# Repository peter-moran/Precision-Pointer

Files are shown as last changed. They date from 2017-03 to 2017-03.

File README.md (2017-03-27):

# Precision Pointer
This repository holds all of the code and hardware files for building a Precision Pointer unit (PPU). This repository is not fully ready to be public, so you may encounter errors or gaps in documentation -- however all the code needed to run the system (other than dependencies) can be found here.

## Building a PPU
Here's the general steps to replicating the system.
1. Buy the materials in `/Hardware Documentation/Bill of materials.csv`
2. Wire and assemble PPU. You will need to create additional mounts for the linear actuator. Again, see the files in the Hardware Documentation folder. See `pointer_driver/pointer_driver.ino` for pin definitions.
3. Connect to ArbotiX in Arduino IDE and upload `pointer_driver.ino`
4. Use `pointer.py` as an API interface to the PPU. `pointer_client.py` is also provided to provide remote control of a PPU connected to a remote machine.

---

# TODO
1. Remove Klampt dependency -- specifically replace `vectorops` operations.
2. Replace servo linear actuator with a digital servo motor. Specifically, use another dynamixel motor and translate the rotational motion to linear motion. This will provide far better consistency and accuracy for linear motion.

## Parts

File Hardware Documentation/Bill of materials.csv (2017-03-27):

Pointer Bill of Materials
Item | Brand | Manufacturer Part # | Source | Link | Count | Unit Price
ScorpionX MX-64 Robot Turret | Trossen Robotics | KIT-SXT-MX64 | Trossen | http://www.trossenrobotics.com/p/ScorpionX-RX-64-robot-turret.aspx | 1 | $749.95
L12 100mm 210:1 Linear Actuator | Firgelli |  | Trossen | http://www.trossenrobotics.com/p/figelli-L12-100mm-210-1-Linear-Actuator.aspx | 1 | $90.00

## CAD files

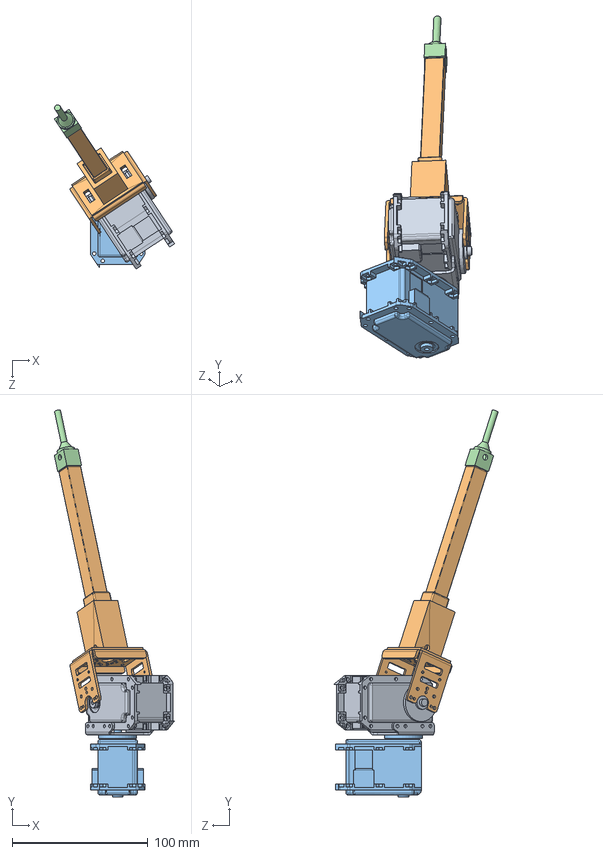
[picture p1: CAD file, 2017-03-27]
Hardware Documentation/Part geometries/Assemblies/Link Assembly.SLDASM
88.6 x 284.9 x 120.9 mm
ppu-link-2
ppu-link-3
MX-64R
IML-PPU-Tip

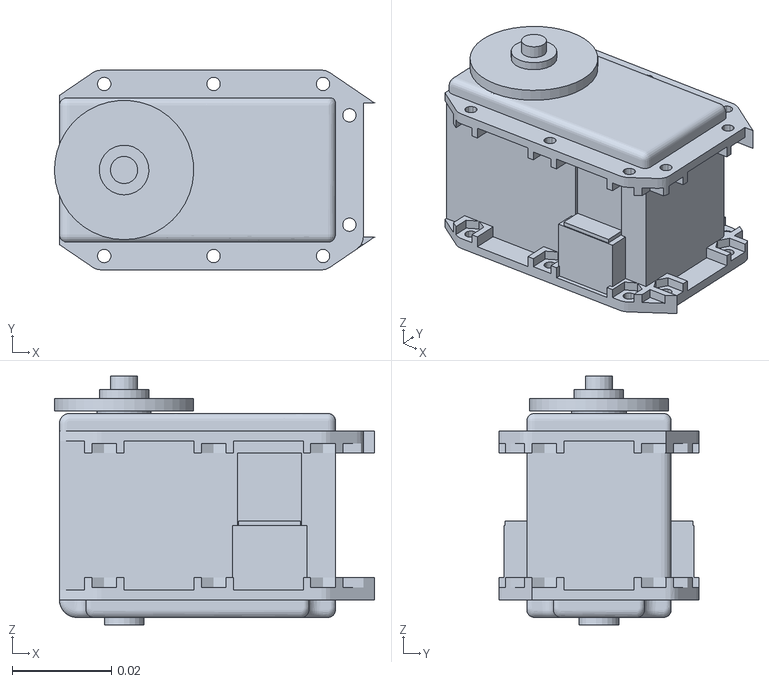
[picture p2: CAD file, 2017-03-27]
Hardware Documentation/Part geometries/Assemblies/Link geometry/ppu-link-1.STL
0.0643 x 0.0402 x 0.05

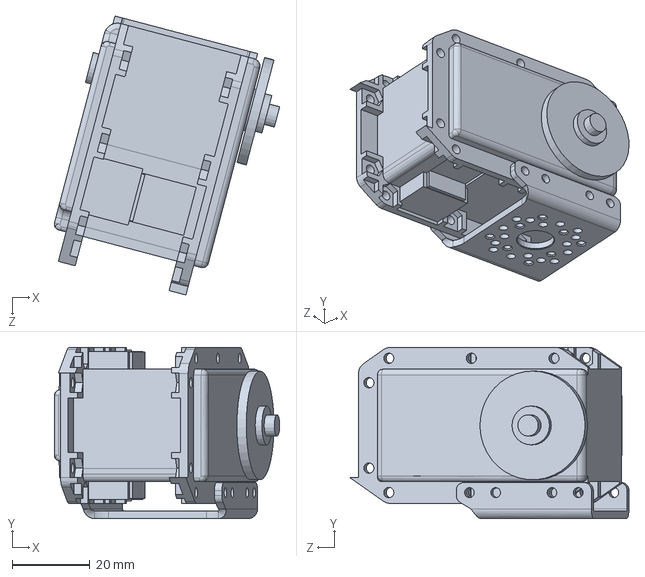
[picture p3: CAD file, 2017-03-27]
Hardware Documentation/Part geometries/Assemblies/Sub-assemblies/ppu-link-2.SLDPRT
58.1 x 44.1 x 71.9 mm

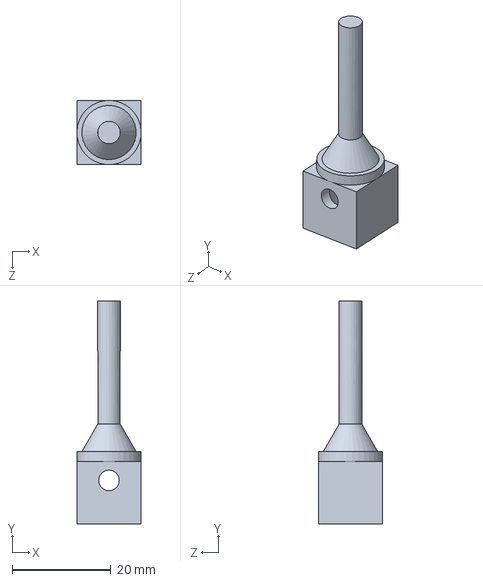
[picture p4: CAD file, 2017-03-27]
Hardware Documentation/Part geometries/Custom Parts/IML-PPU-Tip.SLDPRT
13.0 x 45.2 x 13.0 mm

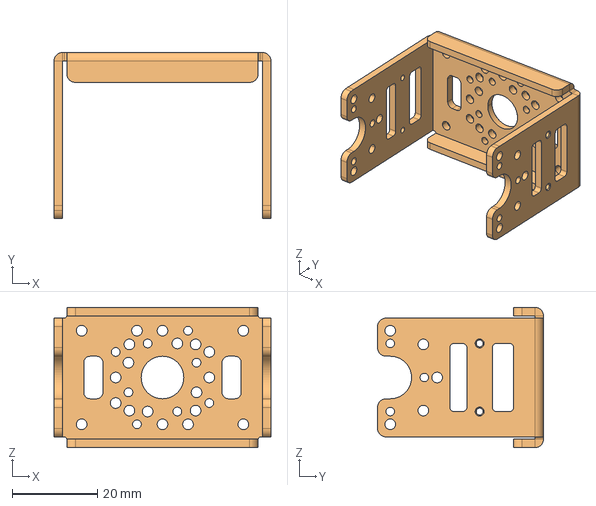
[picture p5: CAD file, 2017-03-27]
Hardware Documentation/Part geometries/Hinge Frame/FR05-H101.stp
51.0 x 39.0 x 33.0 mm

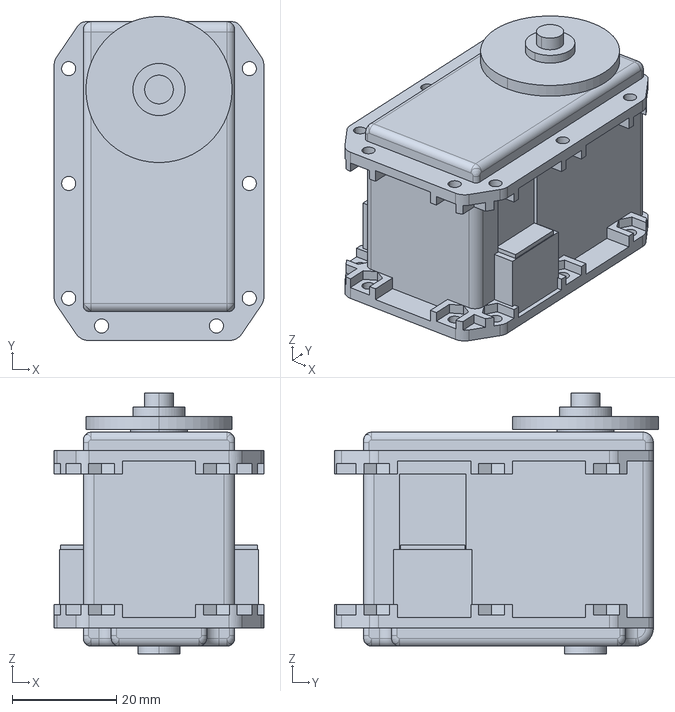
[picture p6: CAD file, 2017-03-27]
Hardware Documentation/Part geometries/MX-64 Servo Motor/MX-64R.stp
40.2 x 62.1 x 50.0 mm

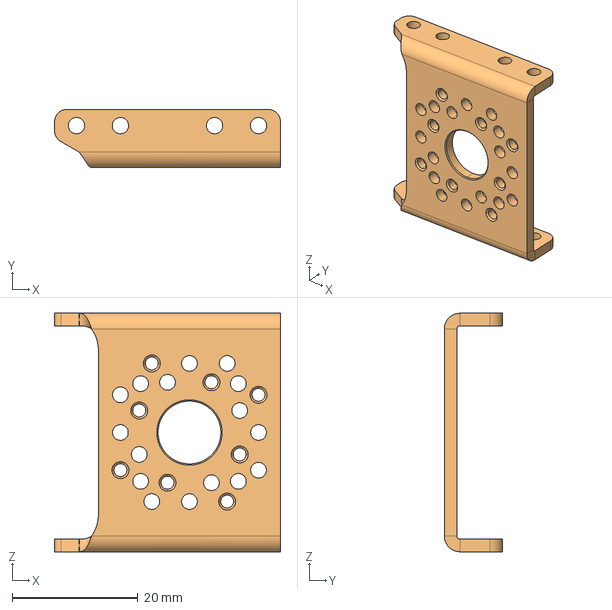
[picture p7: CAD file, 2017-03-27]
Hardware Documentation/Part geometries/Side Frame/FR05-S101.stp
36.0 x 9.30 x 38.0 mm

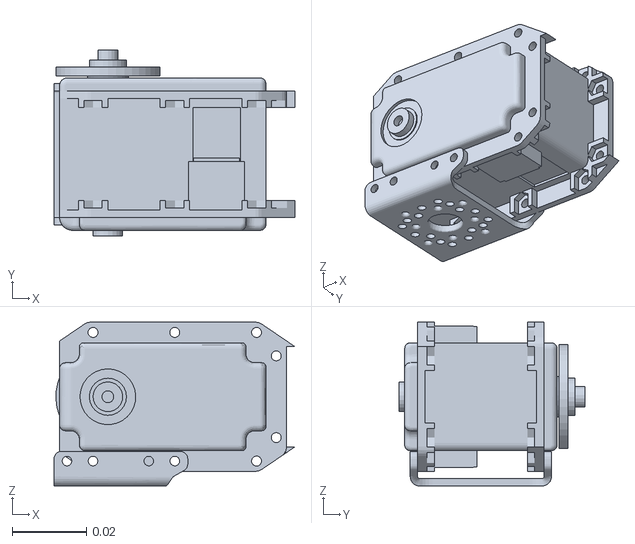
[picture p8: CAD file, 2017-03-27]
Hardware Documentation/Part geometries/Assemblies/Link geometry/ppu-link-2.STL
0.0648 x 0.05 x 0.0441

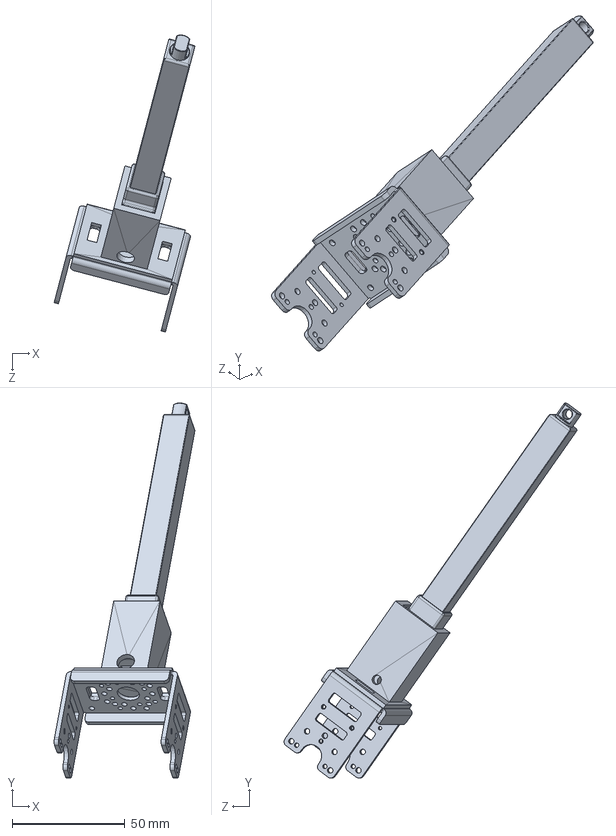
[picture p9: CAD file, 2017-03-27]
Hardware Documentation/Part geometries/Assemblies/Sub-assemblies/ppu-link-3.SLDPRT
62.4 x 166.1 x 131.5 mm

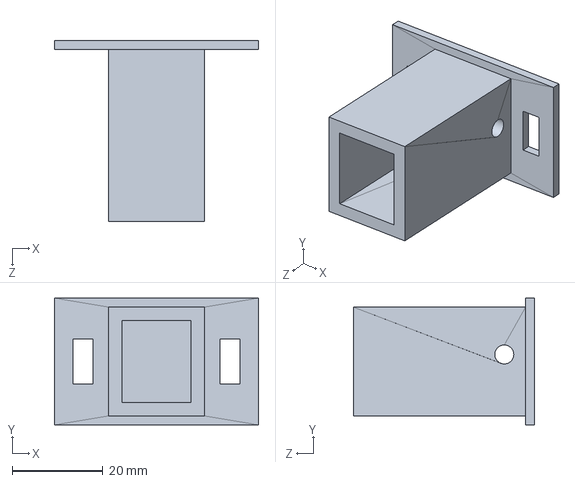
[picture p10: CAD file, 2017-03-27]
Hardware Documentation/Part geometries/Custom Parts/IML-PPU-Base.SLDPRT
45.0 x 28.0 x 40.0 mm

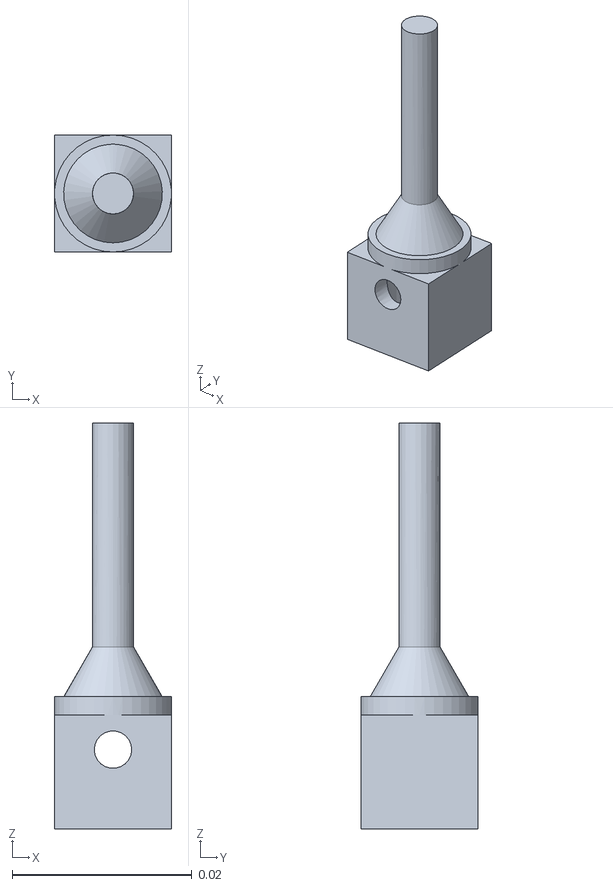
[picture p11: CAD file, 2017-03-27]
Hardware Documentation/Part geometries/Assemblies/Link geometry/ppu-link-4.STL
0.013 x 0.013 x 0.0452

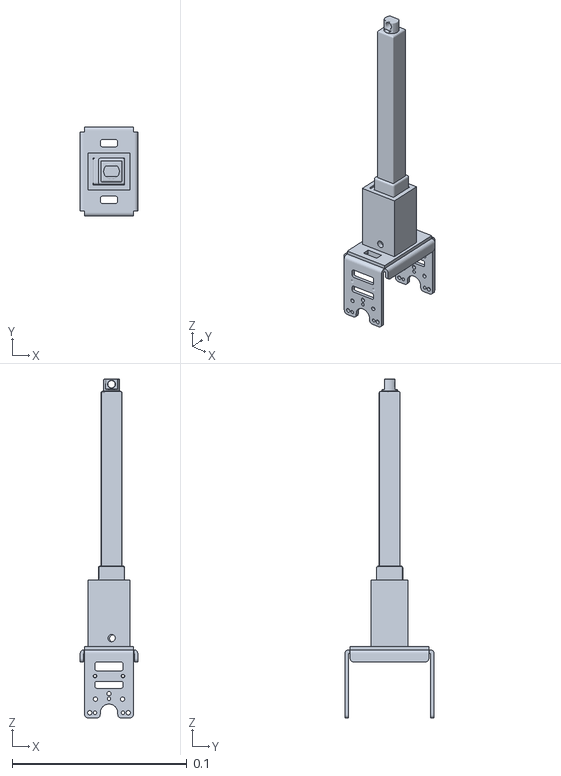
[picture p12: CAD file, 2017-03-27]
Hardware Documentation/Part geometries/Assemblies/Link geometry/ppu-link-3.STL
0.033 x 0.051 x 0.194

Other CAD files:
Hardware Documentation/Part geometries/Custom Parts/IML-PPU-Base.skp
Hardware Documentation/Part geometries/Hinge Frame/FR05-H101.SLDPRT
Hardware Documentation/Part geometries/MX-64 Servo Motor/MX-64R.SLDPRT
Hardware Documentation/Part geometries/Side Frame/FR05-S101.SLDPRT

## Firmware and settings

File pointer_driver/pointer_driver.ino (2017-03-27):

/* 
 By Peter Moran.
 
 Dependencies:
   * Arduino 1.0.6 ( http://learn.trossenrobotics.com/index.php/getting-started-with-the-arbotix/7-arbotix-quick-start-guide )
   * ArbotiX-M Hardware and Library Files
       - IMPORTANT: libraries/Bioloid/ax12.cpp needs to be modified. In ax12SetRegister() and ax12SetRegister2(), uncomment
         the ax12ReadPacket() and make it ax12ReadPacket(6). This will prevent many errors that occur when mixing fast read
         and write speeds.
 
 Notes:
   * Make sure to set menu option "Tools->Board" to "ArbotiX"
   * If first upload does not work, try again. The Arduino should restart (with a chirp!) and then upload the second time.
 
 */

#include <Servo.h> 
#include <BioloidController.h>
#include "packagehandler.h"

///////////////////////////////////////////////////////
///                   Parameters                   ////
///////////////////////////////////////////////////////
// Dynamixel
const int DYNA_MSG_MS = 0;  // time needed between writing/reading to either Dynamixel. Do not set too low.

// Linear actuator
const int LIN_ISMOVE_DZN = 5;

// Messaging
int inByteLens[] = {2,2,2,1,1,2};
int outByteLens[] = {2,2,2,1,1,1};
// extra intialization must be done in packagehandler.h, under "Initalization Parameters"

///////////////////////////////////////////////////////
///             Hardware Definitions               ////
///////////////////////////////////////////////////////
// Dynamixel
BioloidController bioloid = BioloidController(1000000);
const int PAN_ID = 1;   // dynamixel ID of pan motor
const int TILT_ID = 2;  // dynamixel ID of tilt motor
const int CUR_VEL_RGSTR = 38; // register address for reading velocity

// Linear actuator
Servo linac;
const int LINAC_PIN = 12;
const int LIN_FDBK_PIN = 6; // purple wire to A7

// Buzzer
const int BUZZER_PIN = 16;

// Mode codes
const int PASS = 1;   // command to discard data when we recieve it, but continue with requests
const int MOVE = 0;   // for direct control of pan, tilt, ext
const int PRESS = 2;  // for extending until a specified force is detected

///////////////////////////////////////////////////////
///                    State                       ////
///////////////////////////////////////////////////////
PackageHandler hndlr = ConstructPkgHandler(outByteLens, inByteLens, 1000);
int cmdPan;    // long term pan target
int cmdTilt;   // long term tilt target
int cmdExt;    // long term ext target
int stepSize = 30;  // maximum change in written configuration per call of moveDynaTowards()
int mode = 0;  // desired mode based on mode codes
int modeParam;   // parameter to pass to mode (used only in some cases)
int lastWrittenConfig[] = {0, 0};  // last [pan, tilt] values written to Dynamixel registers
unsigned long nextWriteTime[] = {0, 0};  // next time to write to [pan, tilt] Dynamixel registers

///////////////////////////////////////////////////////
///                   MAIN                         ////
///////////////////////////////////////////////////////
void setup(){
  // Beep
  pinMode(BUZZER_PIN, OUTPUT);
  beep();
  
  Serial.begin(115200);
  linac.attach(LINAC_PIN);
  
  delay(50);
  internalHalt();
}

void loop(){
  updateDataOut(&hndlr);
  handleSerialAndPerformOnNewMsg(&hndlr, &processDataIn);
  doCommands();
}

///////////////////////////////////////////////////////
///                     Control                    ////
///////////////////////////////////////////////////////
void doCommands() {
  /* Executes on commands save into State variables. Should be called regularly. */
  if(mode == PRESS) {
    
  }
  else if(mode == MOVE) {
    moveDynaTowards(PAN_ID, cmdPan);
    moveDynaTowards(TILT_ID, cmdTilt);
    setExt(cmdExt);
  }
}

void processDataIn(PackageHandler *hndlr) {
  int newMode = hndlr->dataIn[4];
  if (newMode != PASS && cmdPan != NULL) { // assume full message if cmdPan isnt null. Intended so that nulls are no used on startup, rather than for error checking.
    cmdPan = hndlr->dataIn[0];
    cmdTilt = hndlr->dataIn[1];
    cmdExt = hndlr->dataIn[2];
    stepSize = hndlr->dataIn[3];
    mode = newMode;
    modeParam = hndlr->dataIn[5];
  }
}

void updateDataOut(PackageHandler *hndlr) {
  hndlr->dataOut[0] = getDynaPos(PAN_ID);
  hndlr->dataOut[1] = getDynaPos(TILT_ID);
  hndlr->dataOut[2] = currExt();
  hndlr->dataOut[3] = moving();
  hndlr->dataOut[4] = extVel();
  hndlr->dataOut[5] = linOverload();
}

///////////////////////////////////////////////////////
///                    Movement                    ////
///////////////////////////////////////////////////////
void moveDynaTowards(int id, int pos) {
  /* Commands Dynamixel to move 1 step size in the direction towards the desired configuration. By calling this continually
  untill the desired position is reached, the Dynamixel motors will move at a safe and stable speed */
  unsigned long time = millis();
  int lastPosWrittenToDyna = lastWrittenConfig[id-1];
  if(time >= nextWriteTime[id-1]) {
    // If the step is small enough, go there immediatly
    if((lastPosWrittenToDyna - pos) <= stepSize && (lastPosWrittenToDyna - pos) >= -stepSize) {
      commandDynaTo(id, pos);
    }
    // If step is too large, just go in the right direction
    else {
      if(pos > lastPosWrittenToDyna) {
        commandDynaTo(id, lastPosWrittenToDyna+stepSize);
      }
      if(pos < lastPosWrittenToDyna) {
        commandDynaTo(id, lastPosWrittenToDyna-stepSize);
      }
    }
    nextWriteTime[id-1] = time + DYNA_MSG_MS;
  }
}

void commandDynaTo(int id, int pos) {
  // Sets target position for dynamixel directly to its register
  SetPosition(id, pos);
  lastWrittenConfig[id-1] = pos;
}

void setExt(int pulseWidth) {
  if(pulseWidth < 1000) pulseWidth = 1000;
  if(pulseWidth > 2000) pulseWidth = 2000;
  linac.writeMicroseconds(pulseWidth);
}

void pressTo(int overloadLim) {
  // needs overload function to be fixed
}

void internalHalt() {
  /* Sets goal position to current position, effectivly causing a stop on doCommands().
  In practice, doCommands() needs to be continually called in main loop for halt to work.
  This will be overwritten by the next message recieved, and thus only works in specific cases*/
  cmdPan = getDynaPos(PAN_ID);
  cmdTilt = getDynaPos(TILT_ID);
  cmdExt = currExt();
  lastWrittenConfig[0] = cmdPan;
  lastWrittenConfig[1] = cmdTilt;
  mode = MOVE; // to prevent drifting
  doCommands();
}

///////////////////////////////////////////////////////
///                    Feedback                    ////
///////////////////////////////////////////////////////
void beep() {
  digitalWrite(BUZZER_PIN, HIGH);
  delay(8);
  digitalWrite(BUZZER_PIN, LOW);
}

int currExt() {
  // Emperically determined analog reading to pulse-width command conversion
  int analogLow = 650;
  int pwmLow = 50;
  int analogHigh = 441;
  int pwmHigh = 500;
  return map(analogRead(LIN_FDBK_PIN), analogLow, analogHigh, pwmLow, pwmHigh)+1000; // +1000 is to correct for the different value range when map was emperically found
}

int getDynaPos(int motorID) {
  return ax12GetRegister(motorID,36,2);
}

boolean moving() {
  boolean panMov = ax12GetRegister(PAN_ID, CUR_VEL_RGSTR, 2) != 0;
  boolean tiltMov = ax12GetRegister(TILT_ID, CUR_VEL_RGSTR, 2) != 0;
  int curExt = currExt();
  boolean linacMov = extVel() > LIN_ISMOVE_DZN;
  return (panMov<<2) || (tiltMov<<1) || linacMov;
}

int extVel() {
  // TODO: replace with Kalman filter
  return 0; // for compatability until extension position and velocity are fixed
}

int linOverload() {
  return 0; // for compatability until extension position and velocity are fixed
}
